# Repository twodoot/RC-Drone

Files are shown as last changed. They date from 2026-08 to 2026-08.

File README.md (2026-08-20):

# RC Drone
	
This is a project in which I am making an RC Drone and Controller from scratch with 2 arduino nano ESP32s.  <br>   
Both the Drone and Controller are 3D printed, and assembled with various sized bolts and stand-offs.  <br>  
I'm making this project for personal experience in hardware and software design as it is my first embedded system project. <br>  

Here is a link to a video showing a demo of the drone that I built: [Drone Demo](https://youtube.com/shorts/FMnVdksYT60?si=8YT7XMB2EZSOUAqi)
	
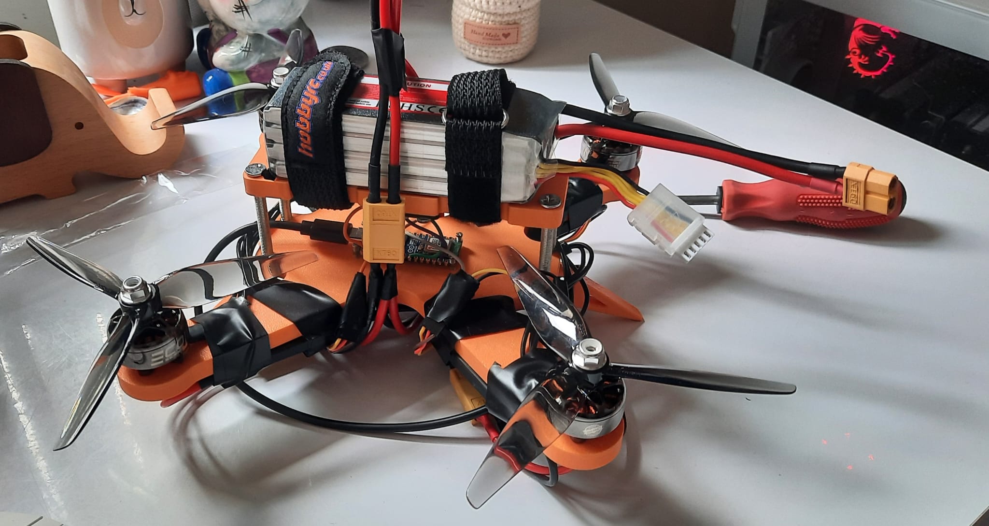
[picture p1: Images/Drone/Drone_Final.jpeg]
 <br> Image of Drone <br> <br>
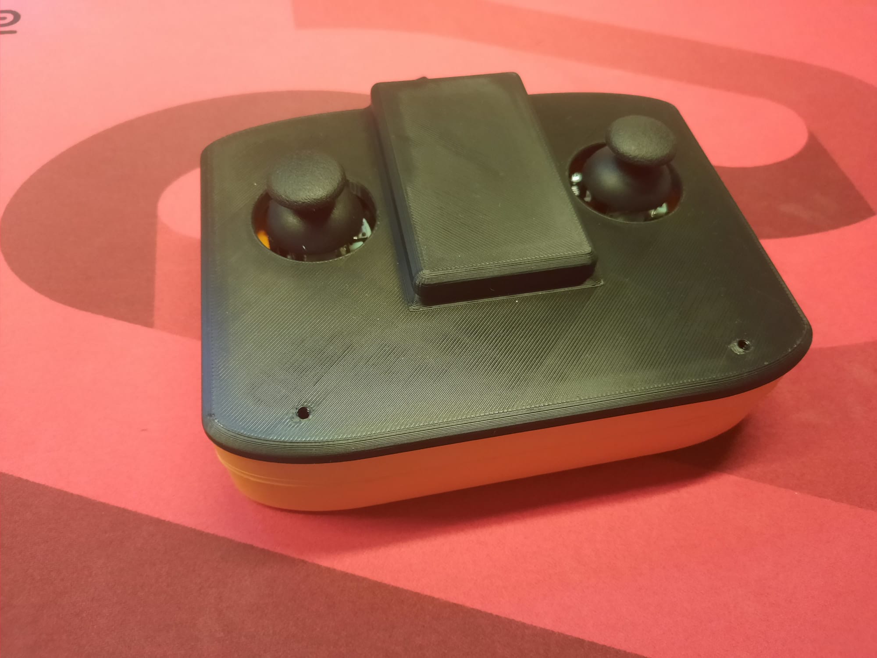
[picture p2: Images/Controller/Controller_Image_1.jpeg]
 <br> Controller with lid <br> <br>
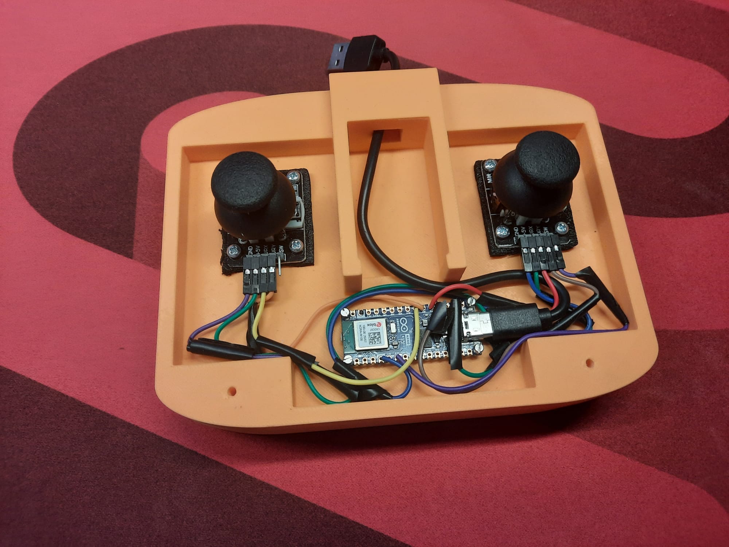
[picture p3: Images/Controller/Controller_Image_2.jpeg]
 <br> Controller without lid <br> <br>
	
## Parts List
	
**3D Printed:**

- Drone Base
- Drone Top 
- Drone legs **x4** 
- Controller Body
- Controller Lid
- Controller Drawer
	
**Electronic Components**
	
- Adruino nano ESP32 without pins **x2**
- MPU-6050
- 4S 2200mah LiPo battery
- XT-60 1 female -> 2 male splitter **x3**
- 5 Volt USB Power Bank (max dimensions: 10.6L x 6.8W x 1.6Th cm)
- Electronic Speed Controller (ESC) at least 40amp rated **x4**
- KY-023 joystick modules **x2**
- jumper wires **many**
- male terminal banana connectors 3.5mm (for soldering not crimping) **x12**
- 2400kv brushless DC motors **x4**
- drone propellers (recommended  5.1x3.6x3) **x4**
- USBC to USBA cable (power and data) **x2**
- Power only USBC to bare wires
	
**Structural**
	
- M1.6 bolts **x8** minimum length 15mm
- M2.5 bolts **x8**
- M3 bolts  **x4** minimum length 18mm
- M3 bolts for motors **x16** minimum length 10mm
- M5 bolts **x4** minimum length 70mm
- electrical tape
- battery straps **x2**
- automotive plastic tubing 1.5mm inner diameter 2.5mm outer diameter for M1.6 stand-offs
- stiff foam (for MPU-6050 and joystick stand-off/ shock absorption)

**Tools**

- sandpaper low grit
- hacksaw
- soldering iron (and solder and a sponge)
- multimeter (for debugging in case you run into issues assembling)
- scissors
- pliers
- screwdriver

## Assembly

### Controller:

Slice and print the Lid and Base of the controller files can be found: Controller CAD Files

Solder wires with female headers onto the relevant pins of the arduino as seen in the wiring diagram below if you are unsure of my following description, ensuring they are large enough to reach the joystick pins when inside the controller but not too much longer so that the wires can fit inside easily, to the A0-A3 and to D3. Then make 2 wires that have 3 way connections stripping a section of casing off the middle off one wire with a female header and soldering another wire with a female header to it. Cover all exposed wires with either heat shrinks (if you have any) or electrical tape (what I did). 

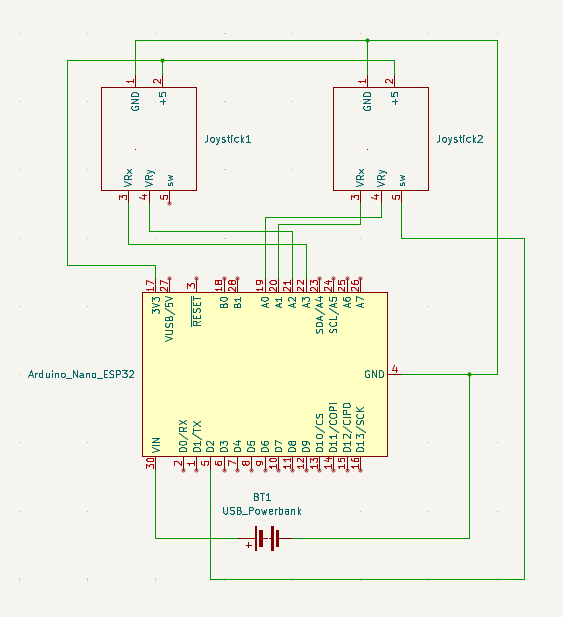
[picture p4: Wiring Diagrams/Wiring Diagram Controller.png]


Extract supports from the controller body:

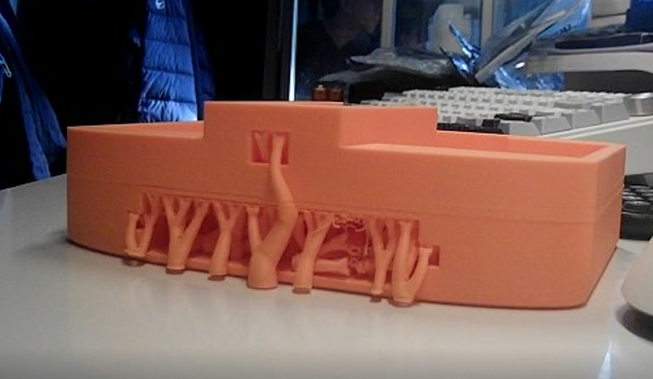
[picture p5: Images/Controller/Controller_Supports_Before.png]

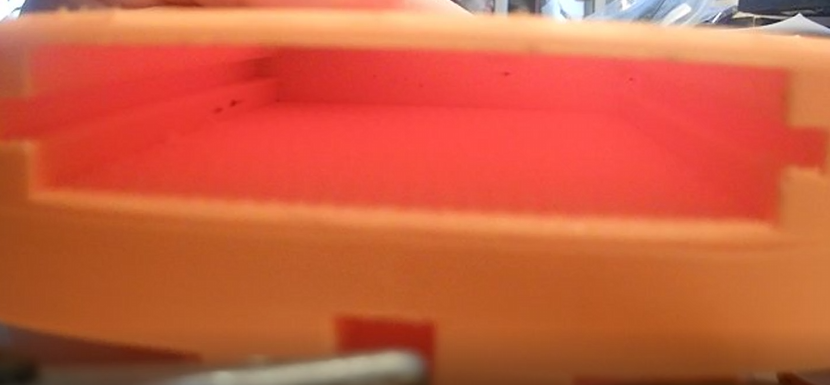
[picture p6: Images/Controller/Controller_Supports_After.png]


Sand down the Drawer until it fits stiffly into the body slot for the power bank underneath but doesn't slide out easily.

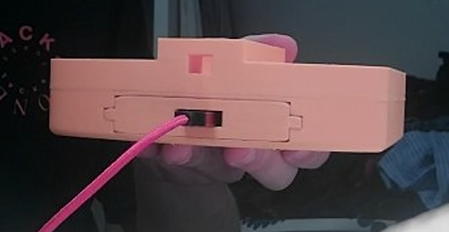
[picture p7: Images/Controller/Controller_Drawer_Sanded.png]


Ensure all exposed bits of wire from soldering are covered up by either electrical tape or shrink-wraps.

Screw in and screw out M1.6 bolts out of the arduino stand-off locations on the controller to widen the tolerances.

Then cut 4 bolts down to size where they will be long enough to screw arduino in well but won't poke through base of controller into the power bank compartment.

Cut off 8 thin bits of the plastic tubing between 1-2mm in length but keep it consistent between the 8.

Fit one stand-off through each M1.6 bolt and then put them on the arduino through the top (USB port is on top) then on the bottom put the other 4 stand-offs sandwiching the arduino between them.

Place the arduino on top of the holes M1.6 holes and screw in the bolts first screwing in all the bolts a small amount until they are all in the threads then taking turns slowly screwing them in until all are screwed in tight and the arduino doesn't wobble.



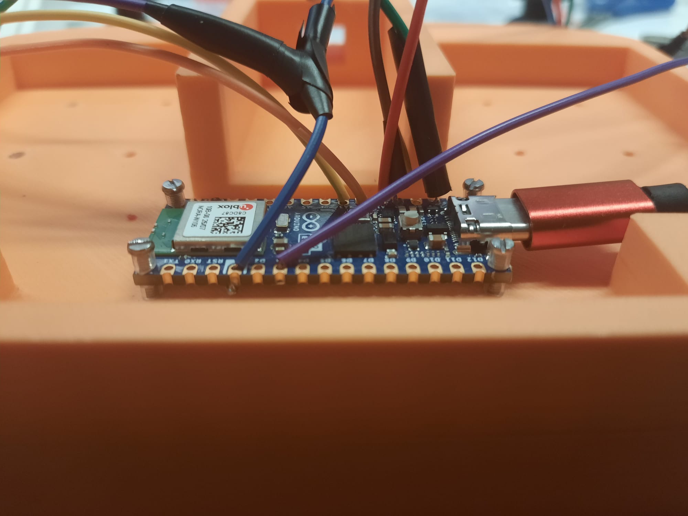
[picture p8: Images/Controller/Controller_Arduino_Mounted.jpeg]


Screw in and out M2.5 bolts a small amount into each mounting hole to widen tolerances and make it easier to screw in joystick modules.

Cut a rectangle of foam around the base of one of the joystick modules then cut it down to only about 3mm thick and repeat for the other one. Thread M2.5 bolts through the mounting holes on each joystick modules and through the foam until it just is about to poke through the bottom then put the joysticks with the attached foam pads on top of the joystick mounting holes and screw them in. Ensure the joystick modules are screwed in with the pins facing the arduino.

Connect the wires up to the joystick modules: GND to GND to each module, 3.3V to +5V to each module, A3 to VRX of left joystick, A2 to VRY of left module, A1 to VRX of right module, A0 to VRY of right joystick, D3 to the SW of right joystick.

Connect a USBC to USBA cable that just reaches the power bank underneath to the slot on the arduino for it.

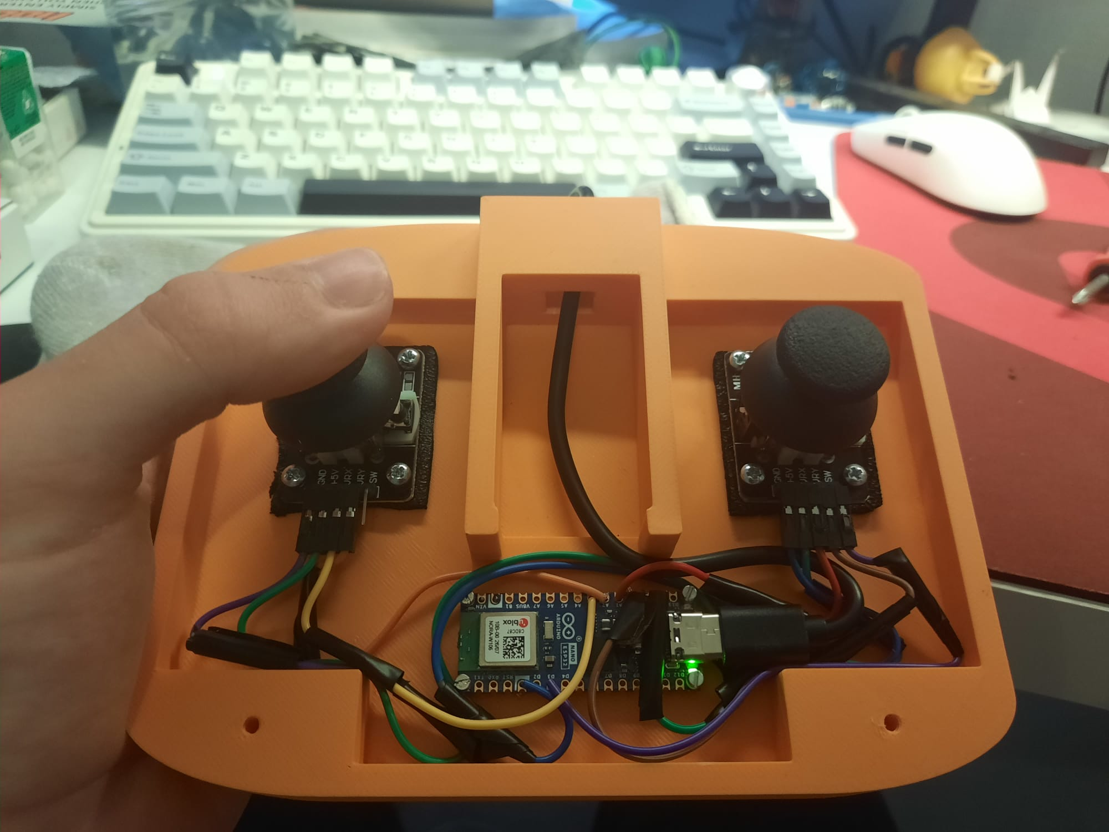
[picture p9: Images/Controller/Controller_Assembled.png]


Optionally the lid can also be put on and even without screws the fit is quite tight so they aren't necessary at all but if you do want to screw it in M3 screws are needed 



### Drone:

Slice and print the Top and Base of the Drone and Spacers: files can be found Drone CAD Files

Connecting the drone arduino and the MPU-6050 IMU: 4 wires will need to be soldered, cut off wire about 20mm long with both ends exposed. Solder one end of the wires onto the MPU-6050 soldering A4 to SDA and A5 to SCL, GND to GND and 3.3V to VCC.

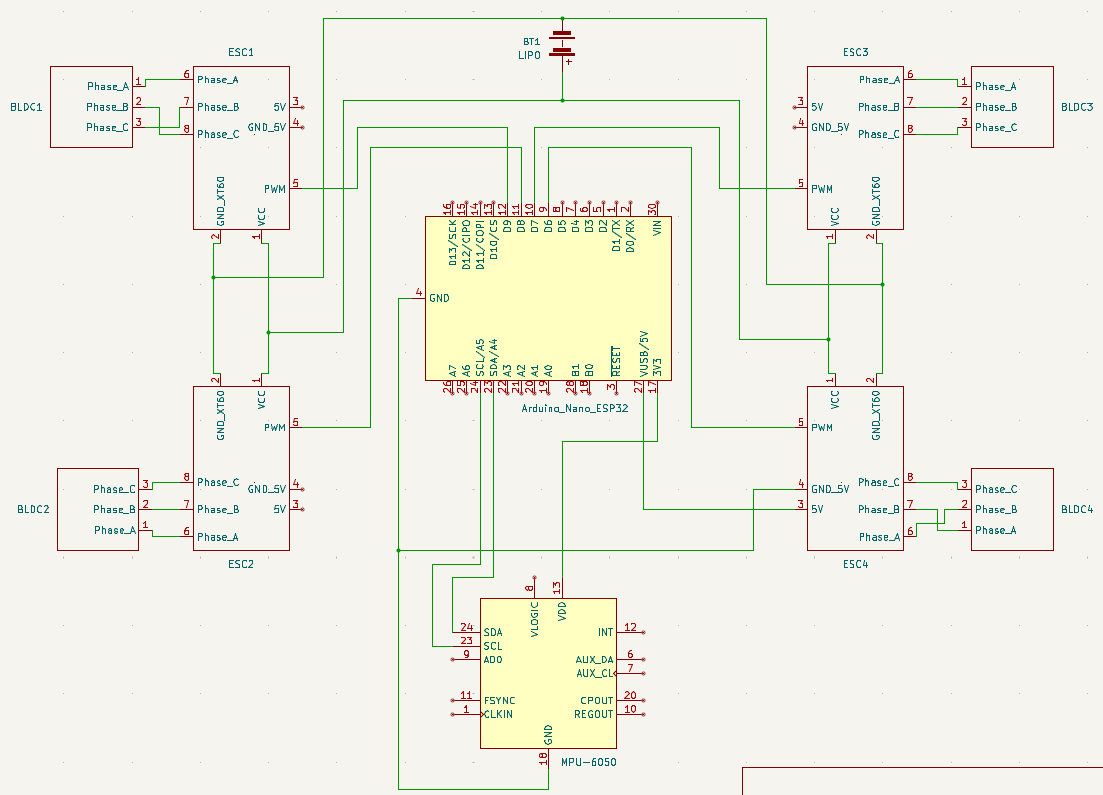
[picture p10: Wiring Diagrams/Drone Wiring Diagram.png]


Screw in M3 bolts to widen the tolerances on the holes for  the mounting of MPU-6050 into drone top part then cut out a piece of the stiff foam to act as a shock absorber and stand-off for the MPU-6050 and screw in the MPU-6050 to the top part of the drone. Ensure that these bolts are cut down to size so that they don't poke out of the top of the drone but fit it perfectly because the battery will be there. To mount the MPU-6050 it should be noted that it should be mounted upside down with the bolts to the right if you are looking at the drone from its rear (USB port of arduino is in rear).

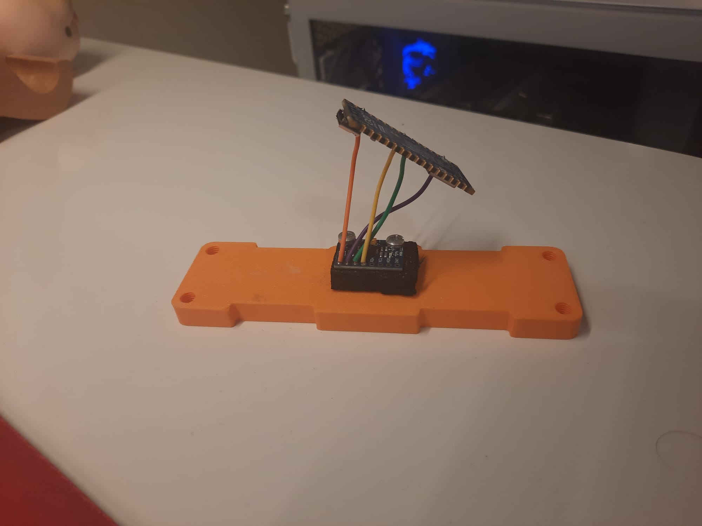
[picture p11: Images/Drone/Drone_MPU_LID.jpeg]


Solder short male header wires onto D6-D9 pins of the drone arduino

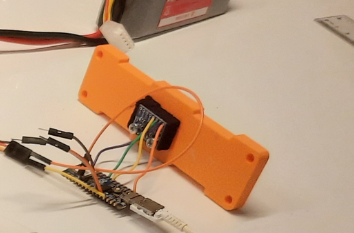
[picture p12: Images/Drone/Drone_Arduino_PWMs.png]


Solder male headers onto the GND and Power wires of the USBC to bare wires cable



Then mount the arduino onto the bottom part of the drone in a method identical to the one previously mentioned with the controller.

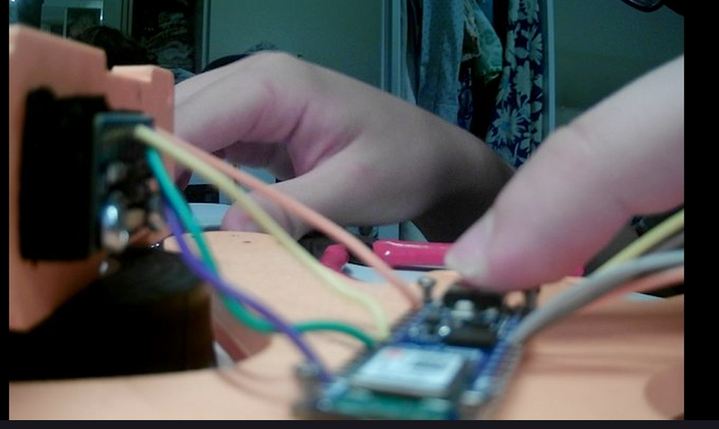
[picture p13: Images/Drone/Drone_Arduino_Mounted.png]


Then insert the M5 70mm into the top of the drone top and screw them down until they around 30mm below the top part with the rest still sticking out the top, then screw them into the base part of the drone until they just don't stick out the bottom, then screw them into the legs which are kept pressed into the bottom until they are screwed in and tighten the bolt to tighten the leg orientation and prevent wobbling.

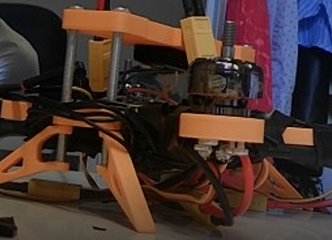
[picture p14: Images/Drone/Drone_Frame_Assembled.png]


Solder 2.5mm male banana connectors to each bare wire of the motor (if not already attached).

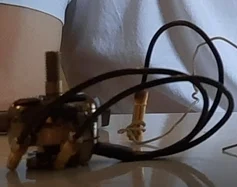
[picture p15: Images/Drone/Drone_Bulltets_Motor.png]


Then also screw in the motors into the base part from the bottom with M3 bolts.

Then tape ESCs under each arm of the base part wiring up the 3 motor wires for each motor to an individual ESC. And wrap electrical tape around each joint to prevent them touching and shorting

Then connect the ESCs power together with the XT-60 1 female -> 2 male splitters connecting the left side with one splitter and the right side with one and connecting them together over the top of the top part of the drone with the third.

Then route the BEC and PWM wires of the ESC through the others to keep them in place at bottom of drone and around the sides to connect into the D6-D9 male headers
also connect the USBC 5 volt and GND to the respective 5 volt and GND of a BEC and around the drone so that it can connect to the drone arduino. Make sure that you also tape these connections (except for the XT-60 ones) to keep them secure

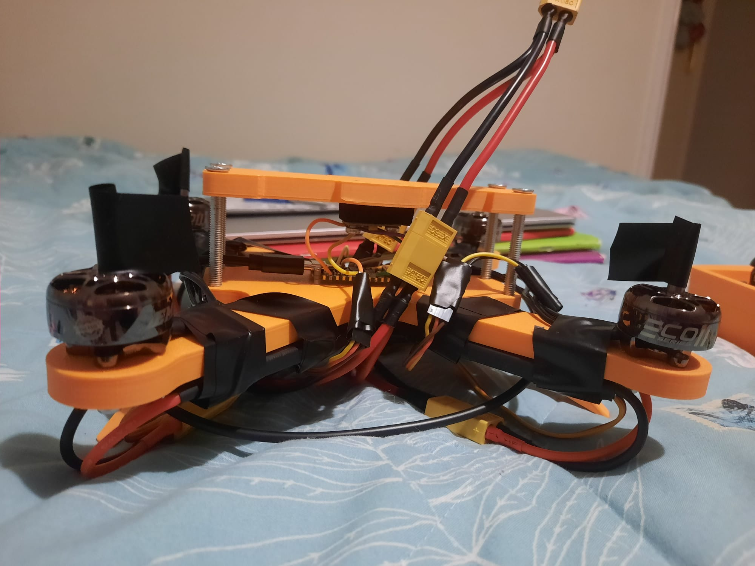
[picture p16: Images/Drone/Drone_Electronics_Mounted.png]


## Code

To flash the code to the arduinos you will need to install Platform IO on VS code
Libraries are already managed by Platform IO in the platformio.ini file.



to flash connect the required arduino to the computer you are on via USB.
Select which file you want to build from the SRC filter by uncommenting it



source code can be found in the src folder but to get all the code as a whole just clone the repo in vscode.

You will need the mac address of your drone arduino to insert into the code manually (in the controller code). This can be done by flashing the GetMacAddress.cpp file to your drone arduino and running it, which will print the mac address of the drone in the serial monitor in a format where it can be simply copy pasted into the controller code.

Then you should calibrate the Controller by running the JoystickGetOffsets.cpp file so all values being sent are 0 when joystick is not being pushed. and these offsets should be input into the offsets for the 2 controller code versions.

flash the ControllerCode.cpp to the controller 

Then flash the bldctest.cpp to the drone arduino to see which motor is which (MOT1 should  be left stick up, MOT2 left stick right,  MOT3 right stick up, MOT4 right stick right) and swap the BEC PWM wires (D6-D9) accordingly until the correct motors get powered by the correct actions.

Then add tape to to each motor to observe its direction of spin. and swap any 2 of the 3 phase connectors between motor and ESC to change direction of spin until MOT1 and MOT4 are counter clockwise and MOT 2 and MOT 3 are clockwise. MOT1 is front left, MOT2 is front right, MOT3 is back left, MOT4 is back right, taking the back to be where the USB port of the drone arduino is.

Then Calibrate the ESCs by powering controller on with ControllerCode.cpp flashed to it with max throttle being held down and then turn on the drone from battery with ESC calibration code flashed to it after the first series of beeps are heard immediately lower throttle stick to 0 and wait until the ESCs stop beeping.

Then flash Drone code to the Drone arduino and flash ControllerCodeAltThrottle.cpp to the controller and with ESCcalibrate.cpp flashed to the drone arduino
the left stick up and down lowers and increases throttle, if let go the current throttle signal is kept, actively needs to be held down to  decrease throttle, left and right on left stick is yaw left and right, right stick left and right is x axis roll left and right, right stick up and down is y roll of drone. In the main flight mode which is the only one that actually functions well from my testing roll rate is controller by stick and drone and in the alternate one which is accessed by pressing down the right stick once will the be the angle based flight mode but i haven’t been able to get it functioning too well so be warned if using it.

Also mount the propellers onto the motors after removing the tape from them and screw the nut as tight as possible so that it doesn’t come out.

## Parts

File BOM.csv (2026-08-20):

Item | Description | Qty | Purchase Link
Drone Base | base of drone 3D printed | 1 | https://github.com/twodoot/RC-Drone/blob/main/CAD%20Files/Drone/Part%20STLs/Drone%20Base.stl
Drone Top | top of drone 3D printed | 1 | https://github.com/twodoot/RC-Drone/blob/main/CAD%20Files/Drone/Part%20STLs/Drone%20Top.stl
Drone legs | top of drone 3D printed | 4 | https://github.com/twodoot/RC-Drone/blob/main/CAD%20Files/Drone/Part%20STLs/Drone%20Landing%20leg.stl
Controller Body | body of controller 3D printed | 1 | https://github.com/twodoot/RC-Drone/blob/main/CAD%20Files/Controller/Part%20Stls/Body.stl
Controller Lid | lid of controller 3D printed | 1 | https://github.com/twodoot/RC-Drone/blob/main/CAD%20Files/Controller/Part%20Stls/Lid.stl
Controller Drawer | drawer of controller 3D printed | 1 | https://github.com/twodoot/RC-Drone/blob/main/CAD%20Files/Controller/Part%20Stls/Drawer.stl
Adruino nano ESP32 | without header pins | 2 | https://www.amazon.co.uk/dp/B0C947C9QS?ref=ppx_yo2ov_dt_b_fed_asin_title
MPU-6050 | Inertial Measurement Unit (IMU) | 1 | https://www.amazon.co.uk/dp/B07XRK5FHP
4S 2200mah LiPo battery | battery for drone | 1 | https://www.amazon.co.uk/dp/B07Y1Q2629
XT-60 splitter | 1 female -> 2 male splitter | 3 | https://www.amazon.co.uk/dp/B0FF1HYT44
USB Power Bank | 5V (max dimensions: 10.6L x 6.8W x 1.6Th cm) | 1 | https://www.amazon.co.uk/dp/B0F6742NVF
Electronic Speed Controller (ESC) | at least 40amp rated | 4 | https://www.amazon.co.uk/dp/B0B4K39KHZ
KY-023 joystick modules | joysticks | 2 | https://www.ebay.co.uk/itm/361695634810
jumper wires | able to also be cut and soldered | many | https://www.amazon.co.uk/dp/B0BZ7PYYLB
male terminal banana connectors | 3.5mm (for soldering not crimping) | 12 | https://www.amazon.co.uk/dp/B0BK68CQ5G?th=1
2400kv BLDCs | brushless DC motors | 4 | https://www.amazon.co.uk/dp/B0DL8NZYLF?th=1
drone propellers | recommended 5.1x3.6x3 | 4 | https://www.hobbyrc.co.uk/hq-headsupfpv-r36-racing-prop-grey
USBC to USBA cable | power and data | 2 | https://www.amazon.co.uk/Anker-Charger-Braided-Standard-Charging/dp/B07DD5YHMH
Power only USBC to bare wires | for soldering | 1 | https://www.amazon.co.uk/dp/B0FHHCRXW2
M1.6 bolts | minimum 15mm | 8 | https://www.amazon.co.uk/dp/B0DJ5G272V
M2.5 bolts | 10mm | 8 | https://www.amazon.co.uk/dp/B0FBMF1L54?th=1
M3 bolts | minimum 18mm for MPU-6050 and controller lid | 4 | https://www.screwfix.com/p/easyfix-bright-zinc-plated-pan-machine-screws-m3-x-20mm-25-pack/5875j
M3 bolts | minimum 10mm for drone motors | 16 | https://www.screwfix.com/p/easyfix-bright-zinc-plated-pan-machine-screws-m3-x-20mm-25-pack/5875j
M5 bolts | 70mm | 4 | https://www.amazon.co.uk/dp/B0D44XBRCD
electrical tape | insulation | 1 | https://www.amazon.co.uk/dp/B074SLM838
battery straps | straps | 2 | https://www.hobbyrc.co.uk/hobbyrc-premium-kevlar-battery-strap-with-metal-catch-250x20mm
plastic tubing | 1.5mm inner diameter 2.5mm outer diameter for M1.6 stand-offs | 1 | https://www.amazon.co.uk/dp/B0CYGR46RG?ref=ppx_yo2ov_dt_b_fed_asin_title&th=1
stiff foam | for MPU-6050 and joystick stand-off/shock absorption | 1 | packaging from one of the items listed here
sandpaper low grit | sanding | 1 | https://www.amazon.co.uk/ProDec-Advance-Resistant-Aluminium-230x140mm/dp/B0DPX4L94B
hacksaw | cutting bolts to size | 1 | https://www.amazon.co.uk/Stanley-Pistol-Grip-Hacksaw-122/dp/B0001IW8TW?rnid=20930948031&rps=1
soldering iron | and solder and a sponge | 1 | https://www.amazon.co.uk/Soldering-Adjustable-Temperature-180-520%C2%B0C-Desoldering/dp/B0CPDGDMD5
armature wire | jig for soldering | 1 | https://www.amazon.co.uk/Aluminum-Bendable-Sculpting-Skeleton-Wrapping/dp/B09C69KZZ1
multimeter | for debugging in case you run into issues assembling | 1 | https://www.amazon.co.uk/dp/B0GJSKBLDJ?th=1
scissors | cutting things | 1 | https://www.amazon.co.uk/KUONIIY-Scissors-Titanium-Comfort-Grip-Multi-Purpose/dp/B0C9PMNC22
pliers | holding down for sawing and screwing | 1 | https://www.amazon.co.uk/Heavy-duty-Professional-Electrical-Diagonal-combination/dp/B0G2XXVMRX
screwdriver | screwing | 1 | https://www.amazon.co.uk/Amazon-Basics-Ratcheting-Electronics-Screwdriver/dp/B07V4TFWFZ

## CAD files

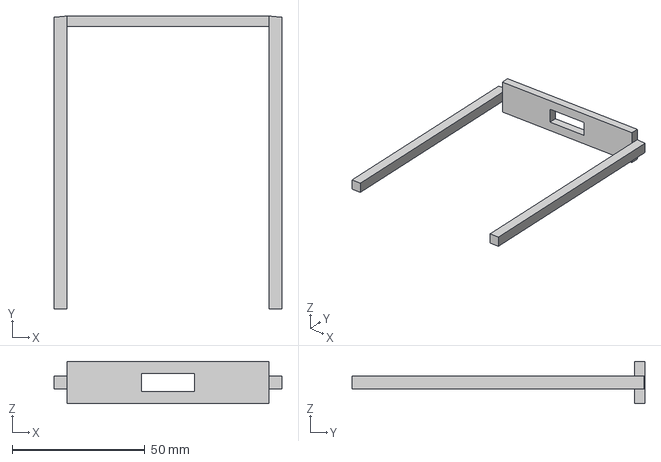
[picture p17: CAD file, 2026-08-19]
CAD Files/Controller/Part STEPs/Drawer.step
85.8 x 110.5 x 15.9 mm

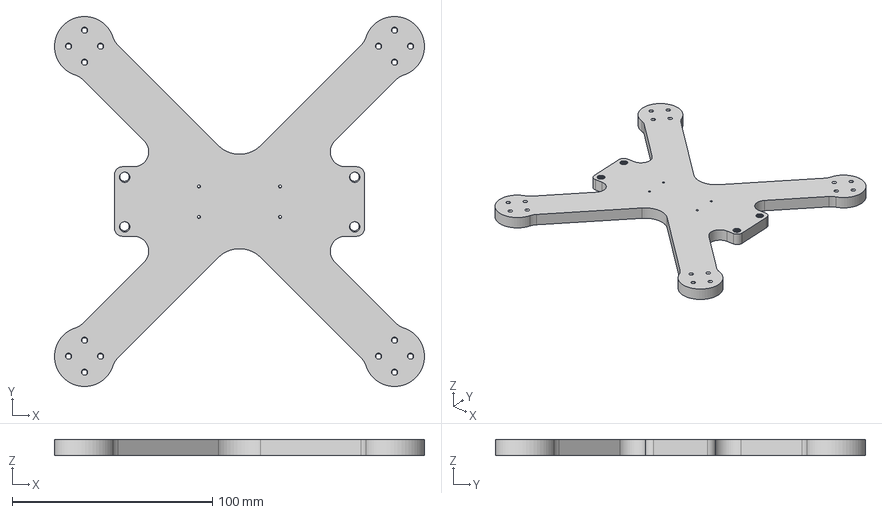
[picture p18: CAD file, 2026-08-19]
CAD Files/Drone/Part STEPs/Drone Base.step
185.0 x 185.0 x 8.00 mm

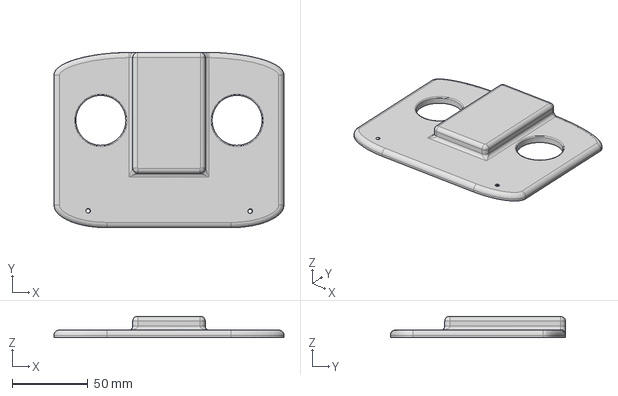
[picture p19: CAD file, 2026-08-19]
CAD Files/Controller/Part STEPs/Lid.step
152.1 x 116.0 x 14.0 mm

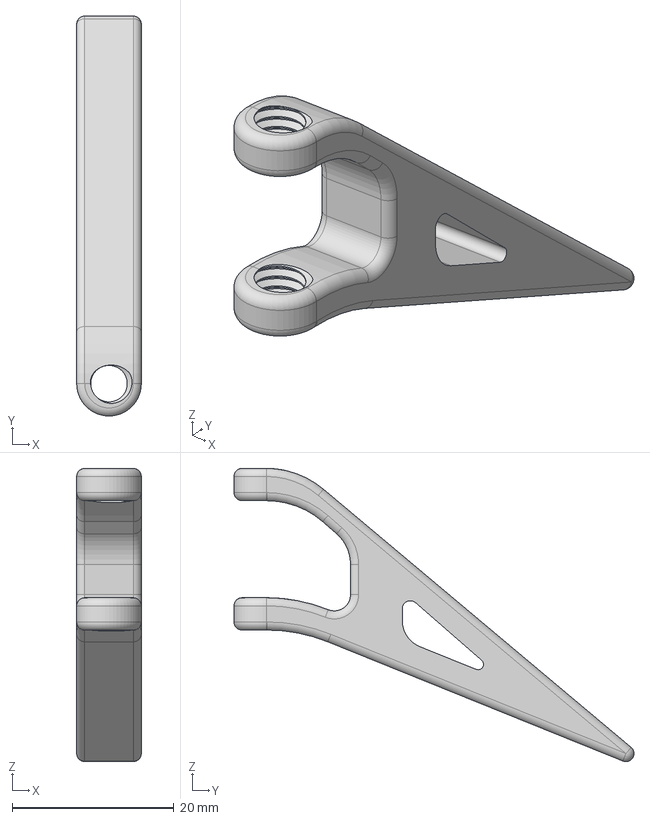
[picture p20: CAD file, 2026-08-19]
CAD Files/Drone/Part STEPs/Drone Landing leg.step
8.00 x 49.5 x 36.3 mm

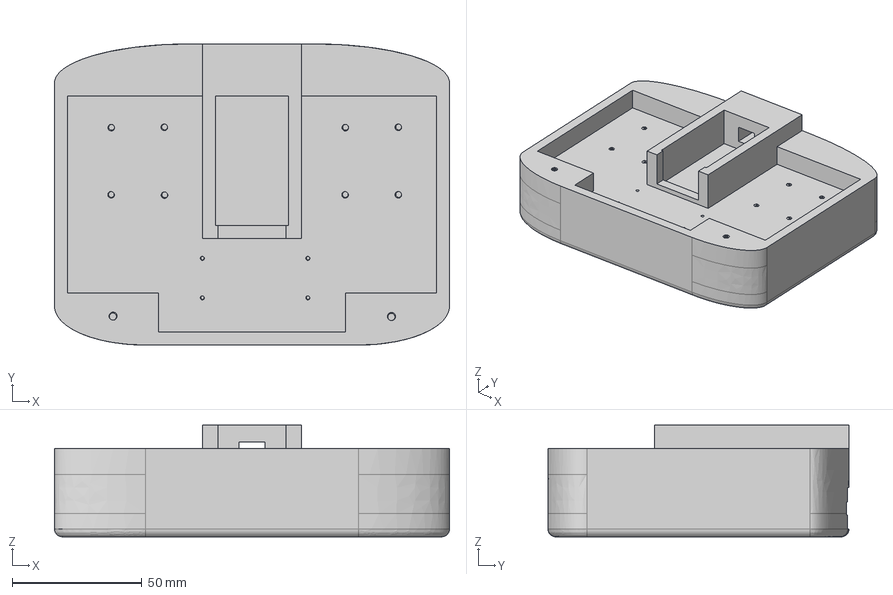
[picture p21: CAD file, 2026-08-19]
CAD Files/Controller/Part STEPs/Body.step
152.1 x 116.0 x 43.0 mm

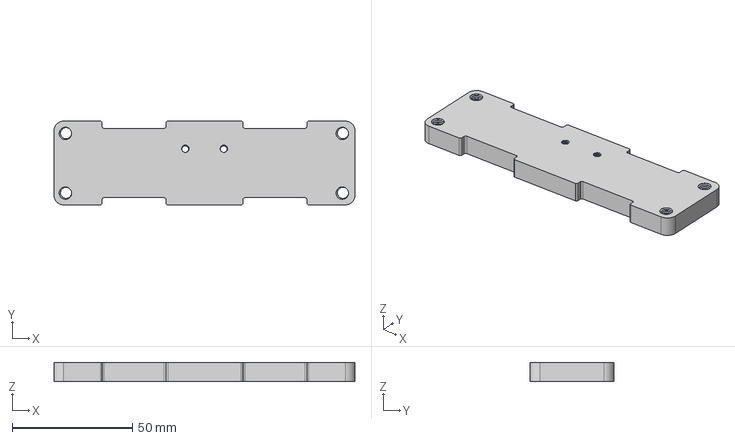
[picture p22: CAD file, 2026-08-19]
CAD Files/Drone/Part STEPs/Drone Top.step
125.0 x 34.8 x 8.00 mm

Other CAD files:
CAD Files/Controller/Part F3d/Body.f3d
CAD Files/Controller/Part F3d/Drawer.f3d
CAD Files/Controller/Part F3d/Lid.f3d
CAD Files/Controller/Part Stls/Drawer.stl
CAD Files/Controller/Part Stls/Lid.stl
CAD Files/Drone/Part F3d/Drone Base.f3d
CAD Files/Drone/Part F3d/Drone Landing leg.f3d
CAD Files/Drone/Part F3d/Drone Top.f3d
CAD Files/Drone/Part STLs/Drone Landing leg.stl
CAD Files/Drone/Part STLs/Drone Top.stl

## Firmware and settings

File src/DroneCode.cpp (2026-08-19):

#include <Arduino.h>
#include <esp_now.h>
#include <WiFi.h>
#include <Wire.h>
#include <Adafruit_MPU6050.h>
#include <Adafruit_Sensor.h>
#include <math.h>
#include <Servo.h>

#define CHANNEL 1

//structs
struct Calibration_Data {
    double a_x, a_y, a_z, g_x, g_y, g_z;

};
struct Roll_Angles {
    double roll_x, roll_y;
};

Servo ESC = Servo();

Adafruit_MPU6050 mpu;
sensors_event_t a, g, t;
Calibration_Data cal;

//other globals
double dt;
double last_time = 10000;

double last_yaw_error = 0;
double last_roll_x_error = 0;
double last_roll_y_error = 0;

//kalman filter
double sigma_gyro = 0.5; //standerd deviation of gyroscope errorin degrees/second
double sigma_accel = 0.118; // standerd deviation of accelerometer error in degrees

double kalman_roll_x_angle = 0, kalman_uncertainty_roll_x_angle = 2*2;
double kalman_roll_y_angle = 0, kalman_uncertainty_roll_y_angle = 2*2;

//constants for PIDs
const double Kp_y = 0.25, Ki_y = 0, Kd_y = 0; //yaw
const double Kp_r_a = 2, Ki_r_a = 0.075, Kd_r_a = 0; //angle
const double Kp_r_g = 0.20, Ki_r_g = 0.04, Kd_r_g = 0; //gyro

//PID Integral cumulative errors
double cumerror_yaw = 0, cumerror_roll_x_a = 0, cumerror_roll_y_a = 0, cumerror_roll_x_g = 0, cumerror_roll_y_g = 0;

//inputs
bool toggle_flight_mode;
int16_t throttle_inp;
int16_t yaw_inp;
int16_t roll_x_inp;
int16_t roll_y_inp;

// funcitons
void OnDataRecv (const uint8_t *mac_addr, const uint8_t *data, int data_len);
double PID (double lasterror, double error, double &Intg, double Kp, double Ki, double Kd);
void KalmanRoll (double &kalman_angle, double &kalman_uncertainty, double gyro_input, double accel_angle);
Roll_Angles Accelerometer_Angle (sensors_vec_t a);
Calibration_Data Calibrate_MPU ();


void setup() {

    //mpu stuff
    Serial.begin(115200);
    mpu.begin();
    mpu.setAccelerometerRange(MPU6050_RANGE_8_G);
    mpu.setGyroRange(MPU6050_RANGE_500_DEG);
    mpu.setFilterBandwidth(MPU6050_BAND_44_HZ);

    //function to calibrate mpu
    cal = Calibrate_MPU();
    cal.a_z += 9.80665;   // + cuz it is upsidedown and remove g from calibration as it stands upright when claibrating

    //esp stuff
    WiFi.mode(WIFI_STA);

    esp_now_init();
    esp_now_register_recv_cb(OnDataRecv);

    //motor arm time
    ESC.writeMicroseconds(17,1000); // MOT1
    ESC.writeMicroseconds(18,1000); //MOT2
    ESC.writeMicroseconds(9,1000); //MOT3
    ESC.writeMicroseconds(10,1000); //MOT4
    delay(5000);
}

void loop() {

    //motor varaibles PWM
    double mot1, mot2, mot3, mot4;

    //time stuff
    double now = millis();
    dt = (now - last_time)/1000;
    last_time = now;

    //getting accel and gyro data
    
    mpu.getEvent(&a, &g, &t);

    a.acceleration.x -= cal.a_x;
    a.acceleration.z -= cal.a_y;
    a.acceleration.z -= cal.a_z;
    g.gyro.x-= cal.g_x;
    g.gyro.y-= cal.g_y;
    g.gyro.z-= cal.g_z;
    
    //need to convert to correct units (degrees)
    
    g.gyro.z = g.gyro.z *180/3.14159;
    g.gyro.x = g.gyro.x *180/3.14159;
    g.gyro.y = g.gyro.y *180/3.14159;

    

    // its upside down when im working with it so i want to treat it like its right way up

    a.acceleration.z *= -1;

    // so its correct for drone

    double temp_swap = a.acceleration.x;
    a.acceleration.x = a.acceleration.y;
    a.acceleration.y = temp_swap;
    a.acceleration.x *= -1;
    a.acceleration.y *= -1;

    temp_swap = g.gyro.x;
    g.gyro.x = g.gyro.y;
    g.gyro.y = temp_swap;
    g.gyro.x *= -1;
    g.gyro.y *= -1;

    Serial.print("gyro (x,y): "); Serial.print(g.gyro.x); Serial.print(", ");
    Serial.print(g.gyro.y); Serial.print("  ");

    


    //throttle
    mot1 = throttle_inp;
    mot2 = throttle_inp;
    mot3 = throttle_inp;
    mot4 = throttle_inp;

    //yaw
    double yaw_error = yaw_inp - g.gyro.z;
    
    double temp_yaw_PID = PID(last_yaw_error, yaw_error, cumerror_yaw, Kp_y, Ki_y, Kd_y);


    //mot 1 front left cc, mot 2 front right c, mot 3 back left c, mot4 back right cc


    mot2 -= temp_yaw_PID; mot3 -= temp_yaw_PID;  // clock mot
    mot1 += temp_yaw_PID; mot4 += temp_yaw_PID; // cclock mot 

    last_yaw_error = yaw_error;

    
    //roll and pitch

    if (!toggle_flight_mode) {
        //gyroflight

        //change integral errors for angle flight to 0
        cumerror_roll_x_a = 0;
        cumerror_roll_y_a = 0;


        //roll x 
        double roll_x_error = roll_x_inp - g.gyro.x;

        double temp_roll_x_PID = PID(last_roll_x_error, roll_x_error, cumerror_roll_x_g ,Kp_r_g, Ki_r_g, Kd_r_g);

        mot2 -= temp_roll_x_PID; mot4 -= temp_roll_x_PID;  // mots on right 
        mot1 += temp_roll_x_PID; mot3 += temp_roll_x_PID; // mots on left

        last_roll_x_error = roll_x_error;

        //roll y
        double roll_y_error = roll_y_inp - g.gyro.y;

        double temp_roll_y_PID = PID(last_roll_y_error, roll_y_error, cumerror_roll_y_g ,Kp_r_g, Ki_r_g, Kd_r_g);

        mot1 -= temp_roll_y_PID; mot2 -= temp_roll_y_PID;  // mots front
        mot3 += temp_roll_y_PID; mot4 += temp_roll_y_PID; // mots rear

        last_roll_y_error = roll_y_error;

    } else {

        Roll_Angles rollangles = Accelerometer_Angle(a.acceleration);

        //change integral errors for gyro flight to 0
        cumerror_roll_x_g = 0;
        cumerror_roll_y_g = 0;
        
        //kalman correceion code (test without first and then try to tune with it if needed)
        
        
        KalmanRoll(kalman_roll_x_angle, kalman_uncertainty_roll_x_angle, g.gyro.x, rollangles.roll_x);
        KalmanRoll(kalman_roll_y_angle, kalman_uncertainty_roll_y_angle, g.gyro.y, rollangles.roll_y);

        rollangles.roll_x = kalman_roll_x_angle;
        rollangles.roll_y = kalman_roll_y_angle;
        

        //roll x

        double roll_x_error = roll_x_inp - rollangles.roll_x;

        double temp_roll_x_PID = PID(last_roll_x_error, roll_x_error, cumerror_roll_x_a ,Kp_r_a, Ki_r_a, Kd_r_a);

        mot2 -= temp_roll_x_PID; mot4 -= temp_roll_x_PID;  // mots on right 
        mot1 += temp_roll_x_PID; mot3 += temp_roll_x_PID; // mots on left

        last_roll_x_error = roll_x_error;

        //roll y

        double roll_y_error = roll_y_inp - rollangles.roll_y;

        double temp_roll_y_PID = PID(last_roll_y_error, roll_y_error, cumerror_roll_y_a, Kp_r_a, Ki_r_a, Kd_r_a);

        mot1 -= temp_roll_y_PID; mot2 -= temp_roll_y_PID;  // mots front
        mot3 += temp_roll_y_PID; mot4 += temp_roll_y_PID; // mots rear

        last_roll_y_error = roll_y_error;


        //kalman debug prints
        Serial.print("kalman roll angles (x,y): ");

        Serial.print(rollangles.roll_x); Serial.print(", "); Serial.print(rollangles.roll_y); Serial.print("  ");
    }

    // turn to pwm signals

    mot1 +=1000;
    mot2 +=1000;
    mot3 +=1000;
    mot4 +=1000;


    if (mot1 <1050) {
        mot1 = 1000;
    }
    if (mot2 <1050) {
        mot2 = 1000;
    }
    if (mot3 <1050) {
        mot3 = 1000;
    }
    if (mot4 <1050) {
        mot4 = 1000;
    }

    if (a.acceleration.z <0) {
        mot1 = 1000;
    }
    if (a.acceleration.z <0) {
        mot2 = 1000;
    }
    if (a.acceleration.z <0) {
        mot3 = 1000;
    }
    if (a.acceleration.z <0) {
        mot4 = 1000;
    }


    mot1 = constrain(mot1 , 1000, 2000);
    mot2 = constrain(mot2 , 1000, 2000);
    mot3 = constrain(mot3 , 1000, 2000);
    mot4 = constrain(mot4 , 1000, 2000);



    //debug prints
    Serial.print("mots 1-4: ");

    Serial.print(mot1); Serial.print(", ");
    Serial.print(mot2); Serial.print(", ");
    Serial.print(mot3); Serial.print(", ");
    Serial.print(mot4); Serial.print(", ");
    
    Serial.println(" ");


    //output 4 different pwm signals
    ESC.writeMicroseconds(17,mot1); // MOT1
    ESC.writeMicroseconds(18,mot2); //MOT2
    ESC.writeMicroseconds(9,mot3); //MOT3
    ESC.writeMicroseconds(10,mot4); //MOT4
    
}

void OnDataRecv (const uint8_t *mac_addr, const uint8_t *data, int data_len) {

    int16_t newdata[5];
    if (data_len == 10) { //nominal message size
        memcpy(newdata, data, sizeof(newdata));

        throttle_inp = newdata[0];
        yaw_inp = newdata[1];
        roll_y_inp = newdata[2];
        roll_x_inp = newdata[3];
        toggle_flight_mode = newdata[4];
    }
    

}

double PID (double lasterror, double error, double &Intg, double Kp, double Ki, double Kd) {

    double Prop = error * Kp;
    Intg += error * dt *Ki;
    double Deri = ((error - lasterror)/ dt ) * Kd;

    return Prop + Intg + Deri;
    
}

void KalmanRoll (double &kalman_angle, double &kalman_uncertainty, double gyro_input, double accel_angle){
    kalman_angle = kalman_angle + (dt * gyro_input);
    kalman_uncertainty = kalman_uncertainty + ((dt * dt) * (sigma_gyro * sigma_gyro));
    double gain = kalman_uncertainty/(kalman_uncertainty + (sigma_accel * sigma_accel));
    kalman_angle = kalman_angle + gain * (accel_angle - kalman_angle);
    kalman_uncertainty = (1-gain)*kalman_uncertainty;
}

Roll_Angles Accelerometer_Angle (sensors_vec_t a) {
    double roll_x;
    double roll_y;
    roll_x  = atan2(a.y,(sqrt((a.x*a.x)+ (a.z*a.z))))*180/3.14159;
    roll_y  = atan2(-a.x,(sqrt((a.y*a.y)+ (a.z*a.z))))*180/3.14159;

    

    Serial.print(roll_x); Serial.print(", ");
    Serial.print(roll_y); Serial.print(", "); Serial.print(", ");
    
    // in case it flips over so it doesnt think its the right way up
    
    /*
    if (a.z <0) {
        if (abs(roll_x)>abs(roll_y)) {
        if (roll_x>0){
            roll_x = 90;
        } else {
            roll_x = -90;
        }}else{

        if (roll_y>0){
            roll_y = 90;
        } else {
            roll_y = -90;
        }}
        
    }*/

    return {roll_x , roll_y};

}

Calibration_Data Calibrate_MPU () {
    sensors_event_t a, g, t;
    //takes 20 readings over 5 seconds and averages

    double a_x = 0, a_y = 0, a_z = 0 , g_x = 0, g_y = 0, g_z = 0;

    for (int i = 0; i < 20; i++) {
        mpu.getEvent(&a, &g, &t);
        a_x += a.acceleration.x;
        a_y += a.acceleration.y;
        a_z += a.acceleration.z;
        g_x += g.gyro.x;
        g_y += g.gyro.y;
        g_z += g.gyro.z;
        
        delay(250);
    }
    a_x /=20; a_y /=20; a_z /=20; g_x/=20; g_y/=20; g_z /= 20;

    return {a_x , a_y , a_z, g_x, g_y, g_z};
}

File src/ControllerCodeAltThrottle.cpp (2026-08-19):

#include <Arduino.h>
#include <esp_now.h>
#include <WiFi.h>

#define CHANNEL 1
#define rollrate_max 40 // gyroscope rollrate maximum in deg/s
#define rollangle_max 15 // accelerometer rollangle maximum in deg
#define yawrate_max 150 // maximum yawrate in deg/s
#define values_per_loop 110 // maximum increase in throttle per 1000 loops

bool toggle_flight_mode = false;
bool lastswitch = HIGH;
bool curswitch;
double throttle;

#define left_y_offset (157.95)
#define left_x_offset (128)
#define right_y_offset (149.5)
#define right_x_offset (130)

double left_y;
int16_t left_x;
int16_t right_x;
int16_t right_y;

esp_now_peer_info_t slave;

void setup() {
  pinMode(6,INPUT_PULLUP);

  WiFi.mode(WIFI_STA);
  esp_now_init();
  uint8_t broadcastAddress[] = {0xE8, 0xF6, 0x0A, 0xC0, 0x4F, 0x20};
  memcpy(slave.peer_addr, broadcastAddress, 6);
  slave.channel = CHANNEL;
  slave.encrypt = false;
  esp_now_add_peer(&slave);
}

void loop() {
  
  left_y = analogRead(4);
  left_x = analogRead(3);

  right_y = analogRead(2);
  right_x = analogRead(1);
  
  left_y += left_y_offset;
  left_x += left_x_offset;
  right_y += right_y_offset;
  right_x += right_x_offset;

  
  left_y = constrain(left_y, left_y_offset , (4095 - left_y_offset));
  left_x = constrain(left_x, left_x_offset , (4095 - left_x_offset));
  right_y = constrain(right_y, right_y_offset , (4095 - right_y_offset));
  right_x = constrain(right_x, right_x_offset , (4095 - right_x_offset));

  
  left_y = map(left_y, left_x_offset, (4095 - left_y_offset), -values_per_loop, values_per_loop);

  if (abs(left_y)> 7){ //avoid random walks
  throttle += (left_y/1000); //to remember for next loop
  }


  throttle = constrain(throttle, 0, 1000);
  left_y = throttle; // for outputing to drone

  left_x = map(left_x, left_x_offset , (4095 - left_x_offset), -yawrate_max, yawrate_max); // deg/s


  curswitch = digitalRead(6);
  if (curswitch == LOW && lastswitch == HIGH) {
    delay(50);
    curswitch = digitalRead(6);
    if (curswitch == LOW ) {
      toggle_flight_mode = !toggle_flight_mode;
    }
  }
  lastswitch = curswitch;

  if (!toggle_flight_mode) {
    // gyro flight
    right_y = map(right_y, right_y_offset , (4095 - right_y_offset), -rollrate_max, rollrate_max); // deg/s
    right_x = map(right_x, right_x_offset , (4095 - right_x_offset), -rollrate_max, rollrate_max); // deg/s
  } else {
    // accelerometer flight
    right_y = map(right_y, right_y_offset , (4095 - right_y_offset), -rollangle_max, rollangle_max); // target angle in deg
    right_x = map(right_x, right_x_offset , (4095 - right_x_offset), -rollangle_max, rollangle_max); // target angle in deg
  }


  Serial.print(left_y); Serial.print(" ,");
  Serial.print(left_x); Serial.print(" ,");
  Serial.print(right_y); Serial.print(" ,");
  Serial.print(right_x); Serial.print(" ,");
  Serial.print(toggle_flight_mode); Serial.println(" ");

  int16_t data[5] = {(int16_t)left_y, left_x, right_y, right_x, toggle_flight_mode};
  esp_now_send(slave.peer_addr, (uint8_t *)data, sizeof(data));
}

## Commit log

2026-05-24 fixed the toggle function
    [ControllerCode.cpp]
2026-05-24 changted switch type to bool
2026-05-29 started work on the flight controller PID system
2026-05-30 added the gyro yaw and roll and pitch code
2026-05-30 made the kalman filter function
2026-06-07 made calibration code
2026-06-07 made accelerometer angle function and the angle control for drone
2026-06-21 added functions to header, fixed z axis caliubration, fixed which motors do x and y roll
    [DroneCode.cpp]
2026-06-22 added length validation ot the receive function and fixed syntax in macaddress funciton
    [DroneCode.cpp, GetMacAddress.cpp]
2026-06-22 fixed the PID function have the intergral term be rememebred between calls
    [DroneCode.cpp]
2026-06-22 fixed first loop having a dt of 5000 milliseconds
    [DroneCode.cpp]
2026-06-23 added the full assembly cad files for the drone and controller
2026-06-23 Added all the other files STL and F3d
    [Controller Body Part.f3d, Controller Lid Part.f3d, Controller Lid Part.stl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]
2026-06-27 added wiring diagrams
2026-06-27 added assembly to readme
2026-06-27 fixed stuff in readme
    Updated minimum lengths for bolts in the structural section and corrected a link for assembly instructions.
